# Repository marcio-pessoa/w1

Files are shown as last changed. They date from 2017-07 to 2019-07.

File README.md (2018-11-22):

# w1 Mark I - Watch Winder

## Introduction
**w1m1** is an acronim to Watch Winder with One slot - Mark I.

A watch winder is a device used to keep automatic watch running when not worn. Automatic watches operate on the principle of winding themselves using a moving weight inside the watch. The weight swings or rotates while the watch is worn and turns the winding mechanism inside the watch. So, fairly obviously, if the watch is not worn, then it no longer receives power this way and will run down. While virtually all automatic watches can be manually wound, this is not always convenient. So the concept of an automatic watch winder was born.

A winder cannot over wind an automatic watch, since all automatic watches have a special mainspring that will never come to the end of the spring. Most winders are on some sort of a timer, so they will operate for a few minutes, then “rest” for a bit, then start their motion again.  There is no need to keep the watch in motion 24 hours.

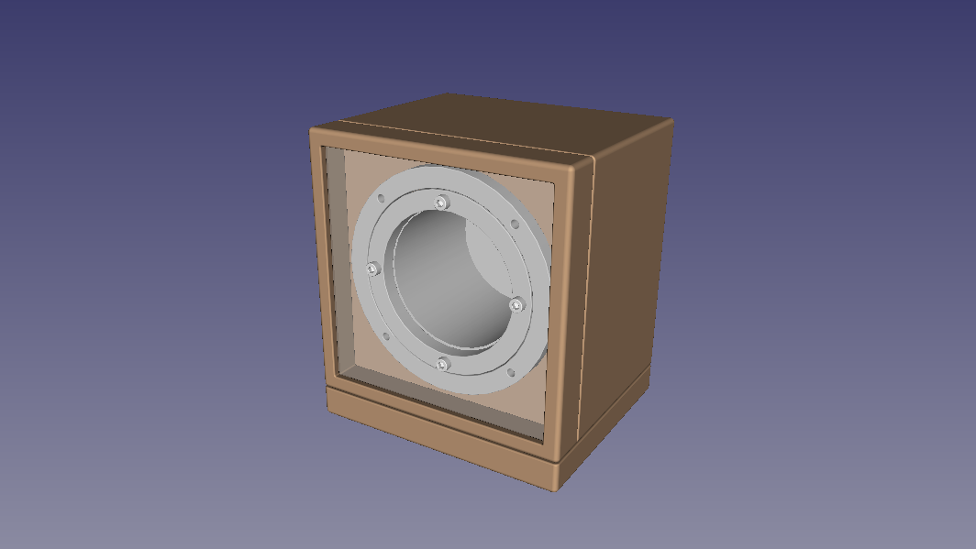
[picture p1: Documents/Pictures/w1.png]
Mechanical design


## Videos
Watch this projects videos on [YouTube Playlist].

## Changes
All notable changes to this project will be documented in this [Change log](CHANGELOG.md).

## Mechanics
This project uses an original mech made from scratch with the following goals:
- Reliable
- Noiseless
- Robust
- Well done
- Cheap, but very beautiful

Check out [Mechanics](Mechanics/README.md) design to know more.

## Electronics
Arduino Leonardo is used with other [Electronics](Electronics/README.md) parts to control the system.

## Firmware
A fully original [Firmware](w1/README.md) was developed to this project.

## BOM - Bill of materials
If you want to build your own, take a look at [Bill of materials](BOM.md).

---
[YouTube Playlist]: https://www.youtube.com/watch?v=WERBobZZHRU&list=PLs1JZHyVhlZXI1KqAdF2J8b70U7dsO11w

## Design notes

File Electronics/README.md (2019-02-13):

# w1 Mark I - Watch Winder

[Main page]

## Electronics

### Arduino
Technical specifications:
- Model: [Arduino Leonardo]

#### Diagram
                                 .-----.
    .----[PWR]-------------------| USB |--.
    |                            '-----'  |
    |                                     |
    |                           A5/SCL[ ] |   C5
    |                           A4/SDA[ ] |   C4
    |                             AREF[ ] |
    |                              GND[ ] |
    | [ ]NC                     SCK/13[ ]~|   B5
    | [ ]v.ref                 MISO/12[ ] |   .
    | [ ]RST                   MOSI/11[ ]~|   .
    | [ ]3V3   +-----+              10[ ]~|   .
    | [ ]5v    |     |               9[ ]~|   .
    | [ ]GND   | MCU |               8[ ] |   B0
    | [ ]GND   |     |                    |
    | [ ]Vin   +-----+               7[ ] |   D7
    |                                6[ ]~|   .
    | [ ]A0                          5[ ]~|   .
    | [ ]A1                          4[ ] |   .
    | [ ]A2                     INT1/3[ ]~|   .
    | [ ]A3                     INT0/2[ ] |   .
    | [ ]A4/SDA  RST SCK MISO     TX>1[ ] |   .
    | [ ]A5/SCL  [ ] [ ] [ ]      RX<0[ ] |   D0
    |            [ ] [ ] [ ]              |
    '--.                         .--------'
       \_______________________/

Arduino Leonardo diagram by http://busyducks.com/ascii-art-arduinos

#### Pin designation
 id | pin |   type    | direction |               description
----|-----|-----------|-----------|--------------------------------------------
  0 |   0 | digital   | input     | Serial communication
  1 |   1 | digital   | output    | Serial communication
  2 |   0 | -         | -         |
  3 |   1 | interrupt | input     | Speed sensor
  4 |   - | -         | -         | -
  5 |   5 | PWM       | output    | Motor (speed control)
  6 |   6 | PWM       | output    | Motor (speed control)
  7 |   - | -         | -         | -
  8 |   - | -         | -         | -
  9 |   9 | -         | -         | -
 10 |  10 | -         | -         | -
 11 |  11 | -         | -         | -
 12 |   - | -         | -         | -
 13 |  13 | PWM       | output    | Status LED
 14 |     | -         | -         | -
 15 |   - | -         | -         | -
 16 |   - | -         | -         | -
 17 |   - | -         | -         | -
 18 |   - | -         | -         | -
 19 |   - | -         | -         | -

### Motor
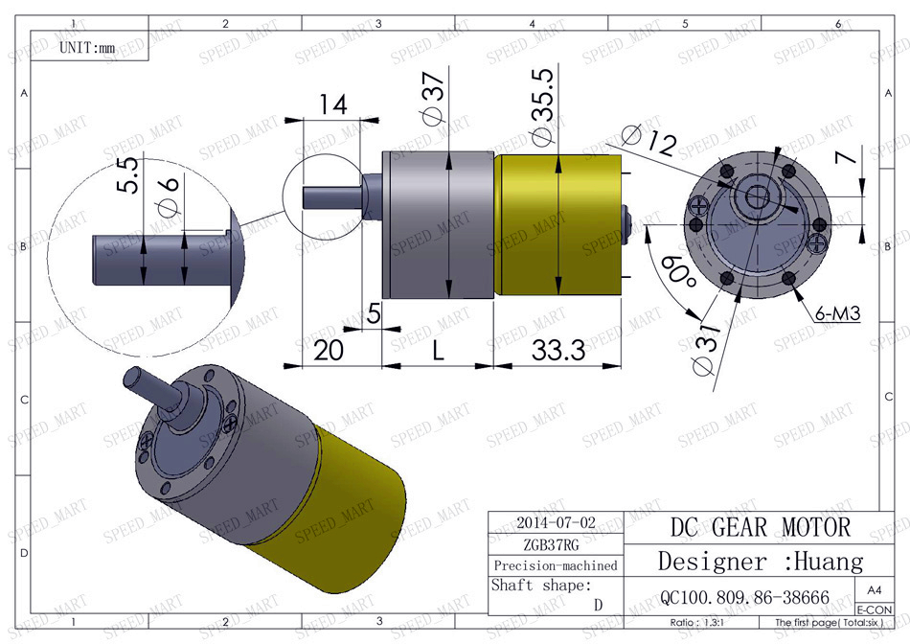
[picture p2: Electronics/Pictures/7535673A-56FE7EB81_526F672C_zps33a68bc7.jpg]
Gear motor


Reversible 37mm 12V DC 100RPM Gear-Box Speed controlled.

Technical specifications:
- Model: ZGB37RG
- Shaft speed: 100 RPM
- Rotor Speed: 5000r/min
- Reversibility: yes
- Voltage: 12V DC
- Current: 800mA (no load)
- Torque: 4kg/cm
- Diameter: 37mm
- Shaft length: 15mm
- Shaft diameter: 6mm

#### Driver
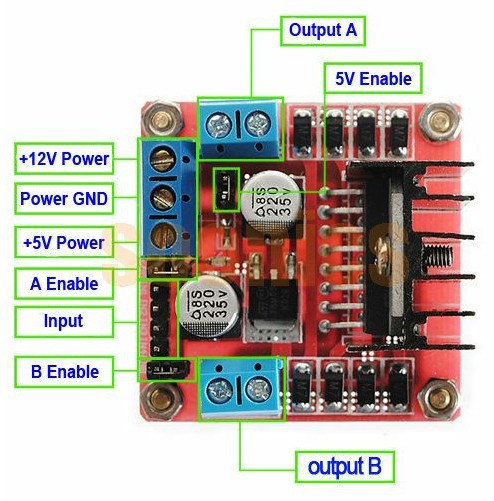
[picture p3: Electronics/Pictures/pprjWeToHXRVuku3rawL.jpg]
L298 motor driver


> "The L298 is an integrated monolithic circuit in a 15-lead Multiwatt and Power SO20 packages. It is a high voltage, high current dual full-bridge driver designed to accept standard TTL logic levels and drive inductive loads such as relays, solenoids, DC and stepping motors. Two enable inputs are provided to enable or disable the device independently of the input signals. The emitters of the lower transistors of each bridge are connected together and the corresponding external terminal can be used for the connection of an external sensing resistor. Anadditional supply input is provided so that the logic works at a lower voltage."
>
> -- From: [L298](../Documents/L298.pdf) data book

L298N absolute maximum ratings:

 Symbol   | Parameter                              | Value      | Unit
----------|----------------------------------------|------------|--------------
 Vs       | Power Supply                           |         50 | V
 Vss      | Logic Supply Voltage                   |          7 | V
 Vi,Ven   | Input and Enable Voltage               |  -0.3 to 7 | V
 Io       | Peak Output Current (each Channel)     |          2 | A
 Vsens    | Sensing Voltage                        |  -1 to 2.3 | V
 Ptot     | Total Power Dissipation (Tcase = 75°C) |         25 | W
 Top      | Junction Operating Temperature         | -25 to 130 | °C
 Tstg, Tj | Storage and Junction Temperature       | -40 to 150 | °C

#### Revolution sensor
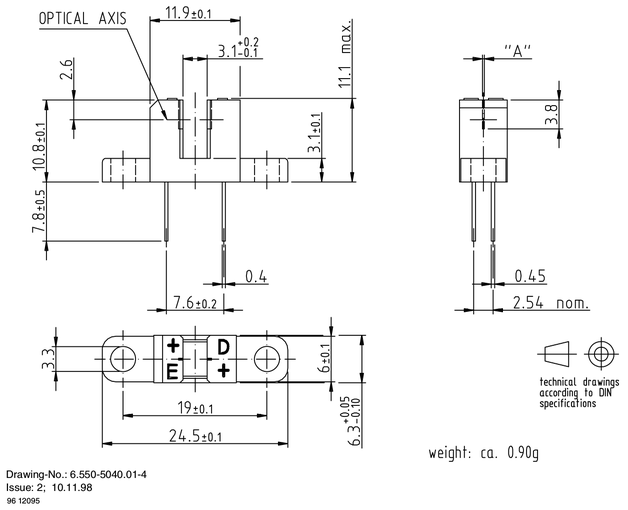
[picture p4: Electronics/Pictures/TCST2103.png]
TCST2103 sensor


> "The TCST2103 is a transmissive sensor that include an infrared emitter and phototransistor, located face-to-face on the optical axes in a leaded package which blocks visible light."
>
> -- From: [TCST2103](../Documents/TCST2103.pdf) data book

### Charger system

#### Qi

### Door sensor
Technical specifications:
- Model: Sensor 44E_938
- Type: Magnetic

[Main page]

---

[Main page]: ../README.md
[Arduino Leonardo]: https://www.arduino.cc/en/Main/arduinoBoardLeonardo/#techspecs

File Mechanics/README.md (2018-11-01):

# w1 Mark I - Watch Winder

[Main page]

## Mechanics

### Case
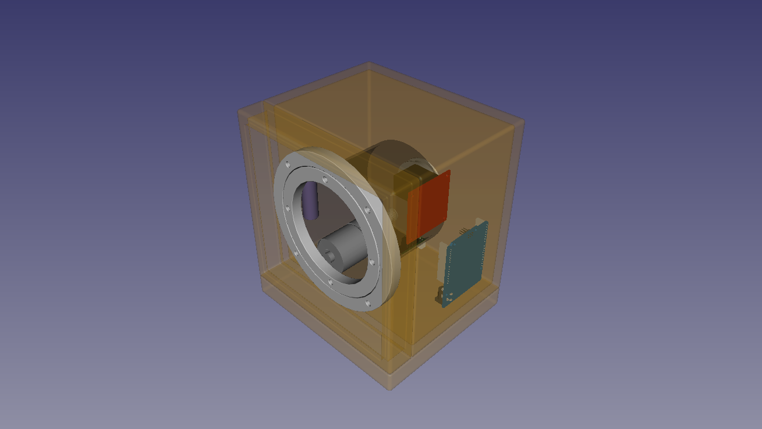
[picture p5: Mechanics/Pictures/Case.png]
Case


Technical specifications:
- Material: Wood
- Feature: Noise reduction with internal fine spounge

### Base
Base

Technical specifications:
- Material: Wood

#### Feet
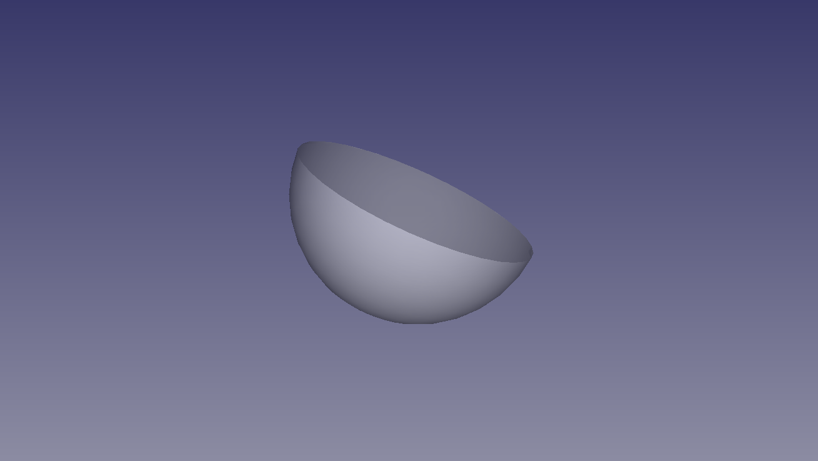
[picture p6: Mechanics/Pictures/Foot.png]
Foot


Technical specifications:
- Material: Silicone
- Feature: Self adhesive
- Color: Transparent
- Diameter: 8 mm
- Height: 2.5 mm

### Engine

#### Pulleys

##### Large
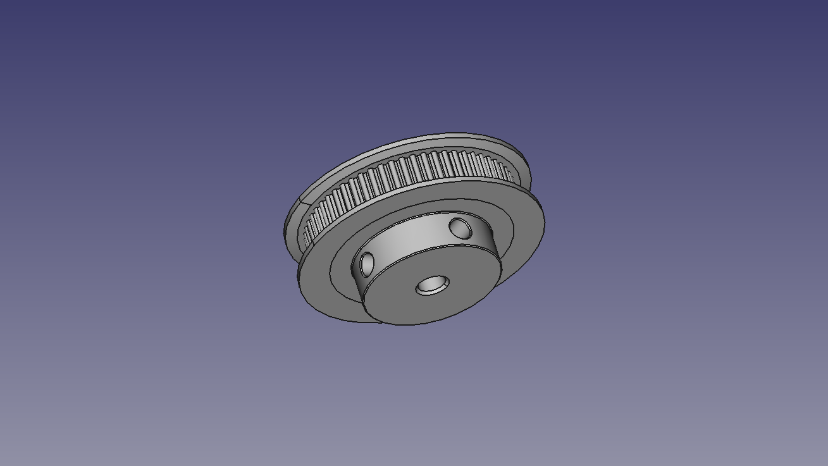
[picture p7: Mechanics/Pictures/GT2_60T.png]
GT2 60T


Technical specifications:
- Model: GT2-60T
- Bore 5mm
- Standard: GT2
- Pinch: 2 mm
- Teeth: 60 T
- Material: Aluminium

##### Small
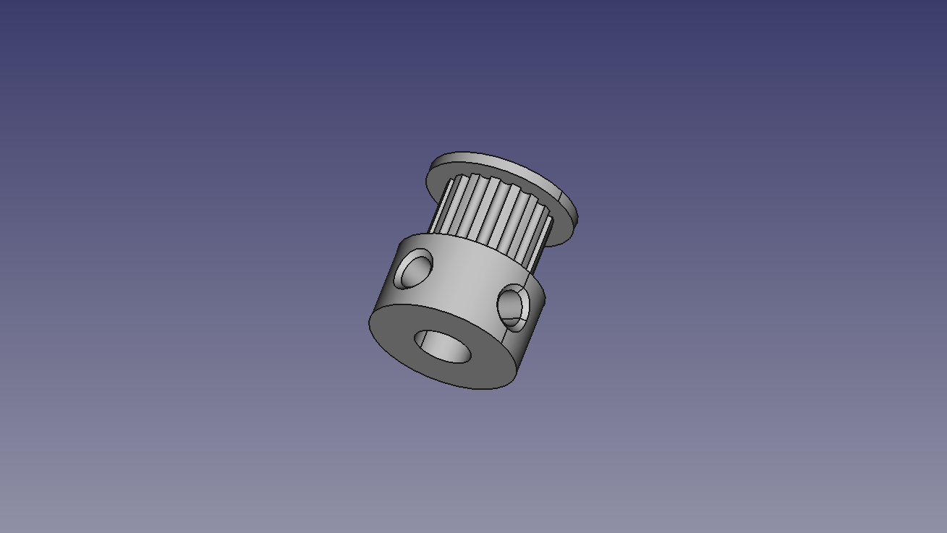
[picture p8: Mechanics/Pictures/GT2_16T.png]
GT2 16T


Technical specifications:
- Model: GT2-16T
- Bore 6mm
- Standard: GT2
- Pinch: 2 mm
- Teeth: 16T
- Material: Aluminium

#### Pulleys relationship
Calculating pulleys relantionship:

$$ s = \frac{B . 100}{A} \% $$

Where:
- A: Large pulley = 60T (Rotor Pulley)
- B: Small pulley = 16T (Motor Pulley)
- s: Speed Ratio = ?

$$ s = \frac{16 . 100}{60} \% $$

So:
$$ s = 26.7 \% $$

#### Wheelbase
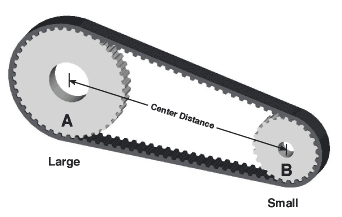
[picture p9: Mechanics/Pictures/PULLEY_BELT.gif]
Center distance


Use trigonometric functions to calculate distance between points A and B.

Using the Pi constant and pulley sizes, it is possible to calculate the belt size and the number of teeth.

Wheelbase data:
- Large pulley (A): 38.2 mm
- Small pulley (B): 10.2 mm
- Center distance: **64.5 mm**
- Teeth in mesh: **6 T**

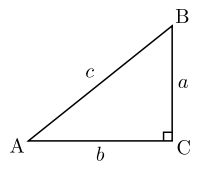
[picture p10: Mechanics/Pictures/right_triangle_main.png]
Right triangle


Reference: https://www.bbman.com/belt-length-calculator/

#### Belt
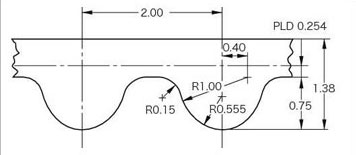
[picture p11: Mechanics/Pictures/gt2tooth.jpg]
GT2 belt


Technical specifications:
- Standard: GT2
- Pinch: 2 mm
- Wide: 6 mm
- Internal lenght: 208 mm
- Teeth: 104 T

#### Lazy Susan
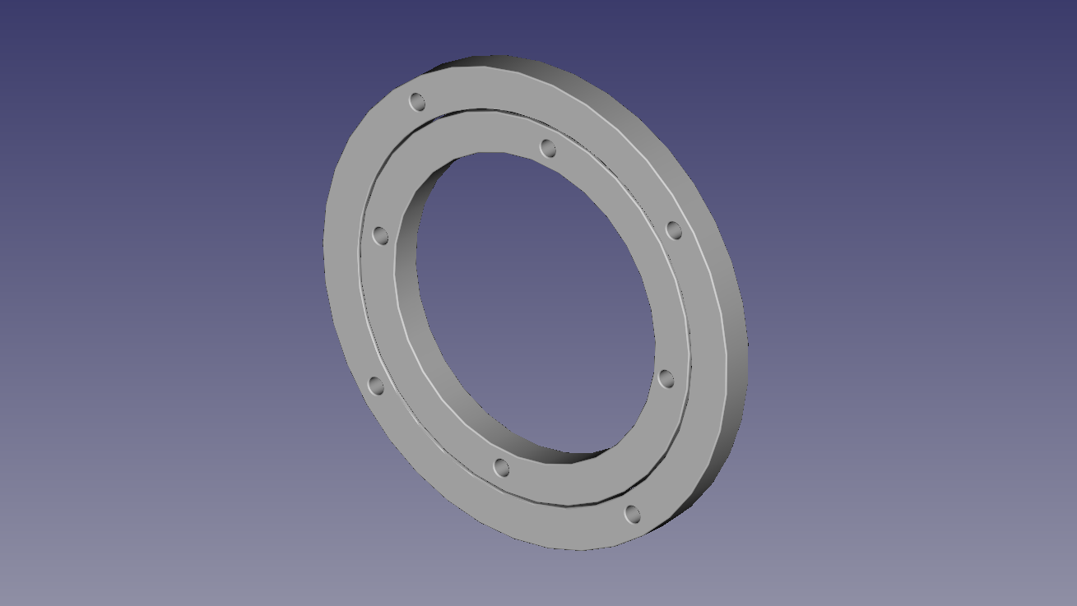
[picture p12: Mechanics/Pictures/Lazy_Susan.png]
Lazy Susan


Technical specifications:
- Material: aluminium
- Move: bearing 
- External diameter: 140 mm
- Internal diameter: 90 mm

#### Cup
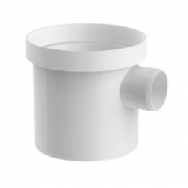
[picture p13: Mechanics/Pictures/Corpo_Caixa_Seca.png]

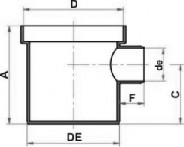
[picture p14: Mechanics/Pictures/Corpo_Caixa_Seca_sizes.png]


Technical specifications:
- Material: PVC
- A: 100 mm
- C: 60.6 mm
- D: 101.6 mm
- DE: 94 mm
- F: 24.8 mm
- de: 37.5 mm

[Main page]

---

[Main page]: ../README.md

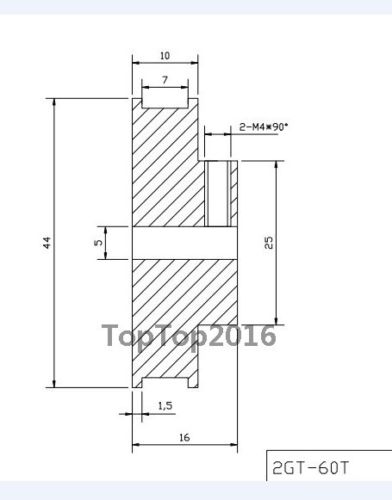
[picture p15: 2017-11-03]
Mechanics/Pictures/GT2 60T.jpg

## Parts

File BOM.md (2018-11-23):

# BOM
w1 Mark I - Watch Winder, Bill of materials

## Purchased
| Quant | Description | ID | Bought | Delivered  | Unit | Charge | Taxes | Cost |
|---|---|---|---|---|---|---|---|---|
| 1 | Arduino_Leonardo | 282612975059 | 2017-08-21 | 2017-10-dd | each | 6.50 |  0.41 | 6.91 |
| 1 | L298N | 192067670930 | 2017-08-21 | 2017-11-dd | each | 1.63 |  0.10 | 1.73 |
| 1 | GT2-16T | 332299393077 | 2017-11-04 | 2017-11-dd | each | 1.99 |  0.13 | 2.12 |
| 1 | GT2-60T | 322570479070 | 2017-08-28 | 2017-mm-dd | each | 3.32 |  0.20 | 3.52 |
| 1 | Lazy_Susan_140mm | 292120279850 | 2017-07-24 | 2017-08-31 | each | 7.14 |  0.44 | 7.58 |
| 1 | GT2_104T_Belt | 162212717993 | 2017-07-27 | 2017-09-19 | each | 2.08 |  0.13 | 2.21 |
| 1 | TCST2103 | 381842310412 | 2016-12-22 | 2017-05-18 | each | 0.80 |  0.05 | 0.85 |
| 1 | ZGB37RG | 261642131158 | 2016-12-26 | 2017-11-01 | each |  15.99 |  1.01 |  17.00 |
| 1 | Platic_cup | - | 2018-01-26 | 2018-01-26 | each | 2.82 |  0.00 | 2.82 |
| 1 | Magnet | - | 2015-mm-dd | 2015-mm-dd | each | 0.00 |  0.00 | 0.00 |
| 1 | Battery | 261530668000 | 2015-05-05 | 2015-mm-dd | each | 1.11 |  0.06 | 1.17 |
| 1 | Battery_case | 263210608095 | 2017-12-03 | 2018-03-29 | each | 0.78 |  0.05 | 0.83 |
| 1 | Qi_receiver | 312013493657 | 2017-12-04 | 2018-04-07 | each | 1.90 |  0.11 | 2.01 |
| 1 | 44E_938 | 181262049602 | 2018-01-01 | 2018-04-18 | each | 0.93 |  0.06 | 0.99 |
| 4 | Silicone_Feet | 182933353181 | 2017-12-27 | 2018-05-28 | each | 0.04 |  0.01 | 0.05 |
| 1 | Qi_charger | 122959306322 | 2018-02-13 | 2018-04-24 | each | 2.83 |  0.17 | 3.00 |
| 1 | Case | - | 2018-04-30 | 2018-04-30 | each | 1.00 |  0.00 | 1.00 |
| 1 | Screw_M5x25mm | 222714655541 | 2017-12-23 | 2018-04-28 | each | 0.20 |  0.02 | 0.22 |
| 5 | Nut_M5_nylon | 222111255325 | 2017-04-25 | 2017-07-dd | each | 0.50 |  0.05 | 0.55 |
| 4 | T-slot_90_corner | 131977551173 | 2016-11-04 | 2016-mm-dd | each | 1.00 |  0.06 | 1.06 |
| 1 | Frame_134x114 | - | 2018-09-28 | 2018-09-28 | each | 0.99 |  0.00 | 0.99 |
| 1 | Frame_125x114 | - | 2018-09-28 | 2018-09-28 | each | 0.99 |  0.00 | 0.99 |
| 4 | T-slot_90*_joint | 163151502873 | 2018-08-18 | 2018-09-27 | each | 1.26 |  0.08 | 1.34 |
| 10 | Screw_M3x8mm_flat  | 253637575896 | 2018-09-30 | 2018-10-23 | each | 0.99 | | |
| 20 | Screw_M3x10mm_flat | 253637575896 | 2018-09-30 | 2018-10-23 | each | 1.07 | | |
| 10 | Screw_M5x20mm_But. | 302874264440 | 2018-10-18 | 2018-11-09 | each | 2.37 | | |
| 1 | Acrylic_Sheet | 292062712986 | 2018-10-23 | 2018-11-19 | each | 6.28 | | |
| 1 | Base | Pending | Pending | pending | each | | | |
| 1 | Door | Pending | Pending | pending | each | | | |
| 1 | Door_glass | Pending | Pending | pending | each | | | |
| 1 | Sponge_adhesive | Pending | Pending | pending | each | | | |
| 1 | Velvet_feet | Pending | Pending | pending | each | | | |

Currency: USD

International IOF: 6.38%
Domestic IOF: 0.38%

Total cost: $58.94

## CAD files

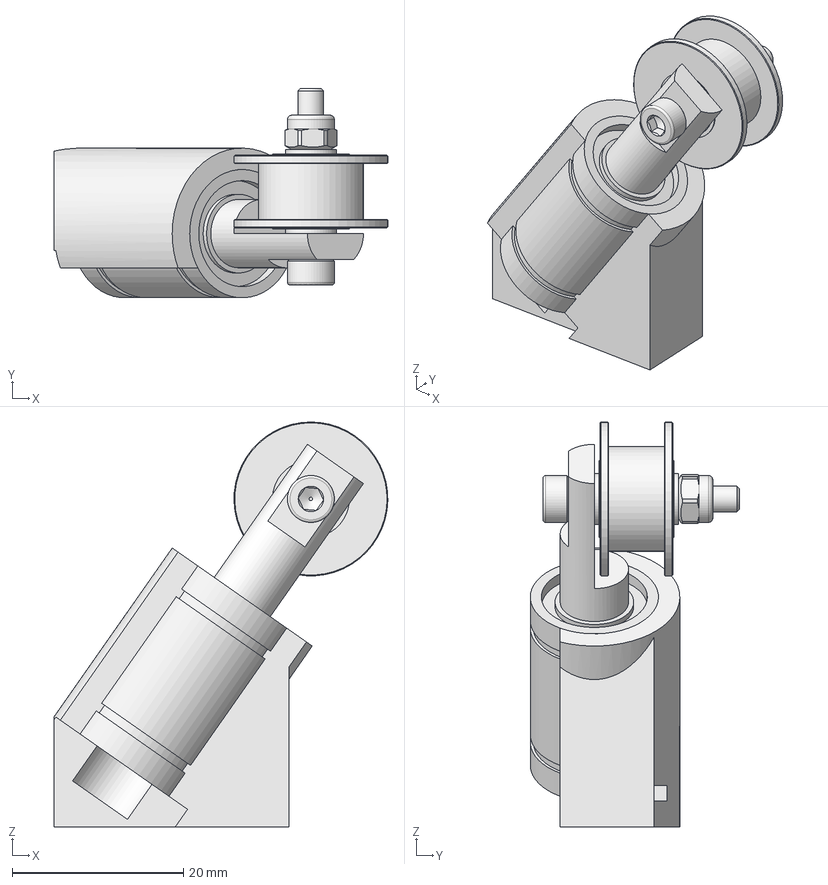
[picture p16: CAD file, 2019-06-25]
Mechanics/Linear_GT2_Belt_Tensioner.FCStd
39.0 x 24.5 x 47.4 mm
M3x20-Screw
M3-Washer_axis_in
M3-Nut_axis
M3-Washer
GT2 20T Smooth 5mm Bore
Piston
LM8UU
M3-Nut

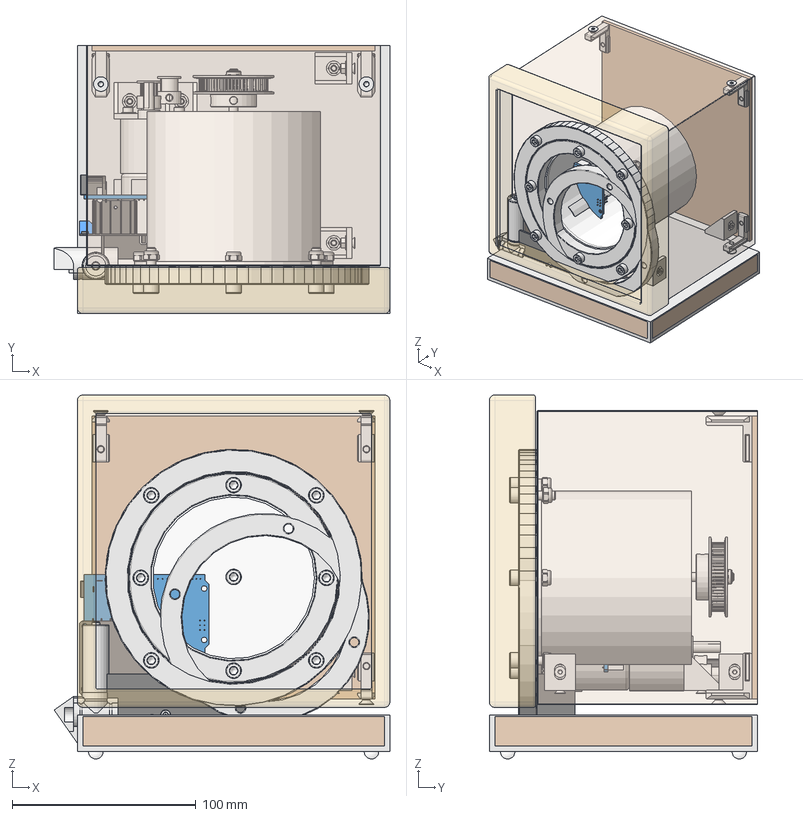
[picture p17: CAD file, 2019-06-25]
Mechanics/w1.FCStd
182.6 x 146.0 x 198.1 mm
Foot_001
Foot_002
Foot_003
Foot_004
CloneScrew001
CloneScrew002
CloneScrew003
CloneScrew004
CloneScrew005
CloneScrew006
CloneScrew007
CloneScrew008
Screw_001
Screw_002
Screw_003
Screw_004
Nut_001
Nut_002
Nut_003
Nut_004
Washer_001
Washer_002
Washer_003
Washer_004
Washer_005
Washer_006
Washer_007
Washer_008
Screw_006
Screw_005
Screw_008
Screw_007
Nut_007
Nut_008
L_005
L_004
L_001
L_002
M5-Nut_000
M5-Nut_001
M5-Nut_002
M5-Nut_003
M5-Nut_004
M5-Nut_005
M5-Nut_006
M5-Nut_007
M5-Nut_008
R6_bat
GT2 20T Smooth 5mm Bore
GT2 16T
GT2 16T_001
Piston
Base_001
Lazy Suzan In Fillet
Lazy Suzan Out Fillet
Door_
Lazy_Susan
Cup
M3-Nut_axis
10 pins-019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

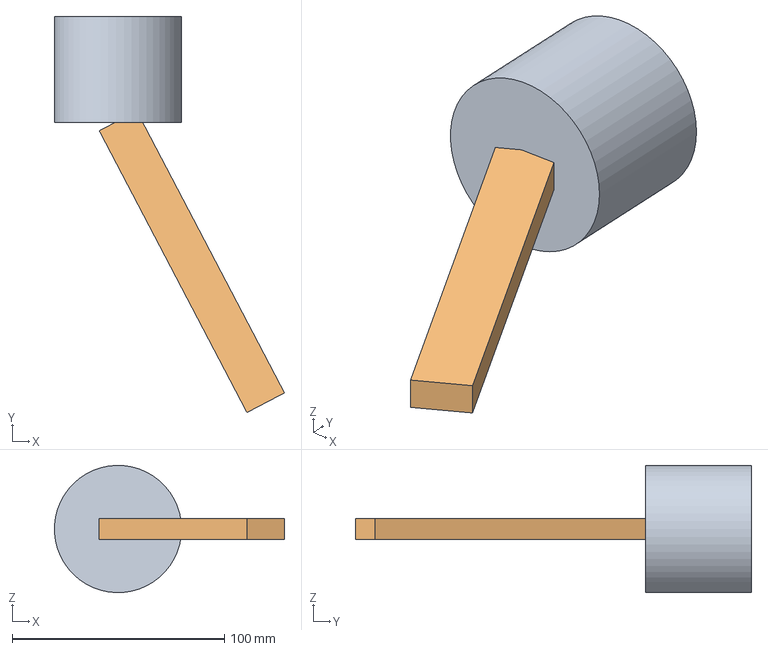
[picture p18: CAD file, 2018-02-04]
Mechanics/crank.FCStd
108.4 x 186.8 x 60.0 mm

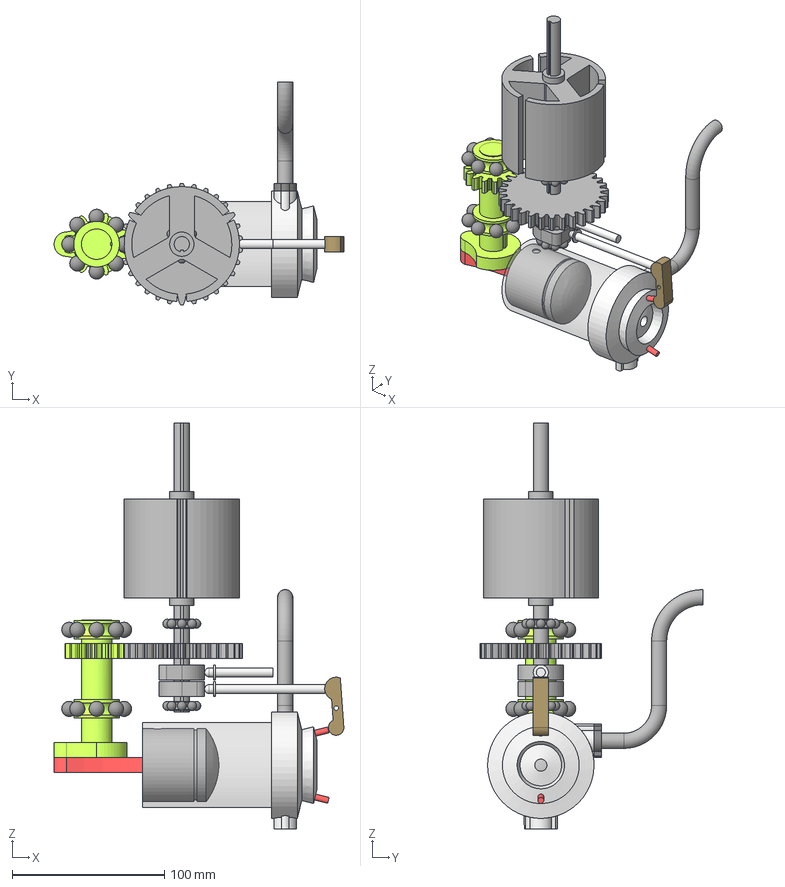
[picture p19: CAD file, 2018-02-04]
Mechanics/Mechanism.FCStd
190.6 x 146.7 x 267.0 mm
MainCylinder
PistonFinal
ConnRodFinal
Balls1
MainShaft
Balls2
HeadFinal
ScapeValve
IntakeValve
SecondaryShaft
Valve2RodFinal
Pipe
PipeHolder
Valve1RodFinal
ExaustValveLeverFinal

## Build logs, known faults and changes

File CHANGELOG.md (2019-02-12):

# CHANGELOG
w1 Mark I - Watch Winder, Change log

## [0.4] - 2017-12-26
### Added
- S command to set rotor speed.

## [0.4] - 2017-12-26
### Fixed
- Minor updates.

## [0.3] - 2017-11-12
### Fixed
- Minor updates.

## [0.2] - 2018-10-22
### Fixed
- Minor updates.

## [0.1] - 2017-11-04
### Added
- Working prototype.

## [0.0] - 2017-07-21
### Added
- The idea.

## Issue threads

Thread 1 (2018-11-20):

M3

marcio-pessoa, 2018-11-20:

marcio-pessoa, 2018-11-20:
This command isn't working properly:
```
M3
Rotor direction: Rotor speed: 100.00 %
nok
```

marcio-pessoa, 2018-12-27:
Problem fixed.

Closed 2018-12-27.

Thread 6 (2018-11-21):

Mechanics - Motor - Fix T-slot_90_corner

marcio-pessoa, 2018-11-21:

Closed 2018-12-27.

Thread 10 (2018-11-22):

Mechanics - Belt - Stress

marcio-pessoa, 2018-11-22:

marcio-pessoa, 2018-12-28:
Quando estava concluindo o Issue #34 percebi que seria necessário um tensionador.

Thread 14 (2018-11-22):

Mechanics - Frame - Design - Fix battery size

marcio-pessoa, 2018-11-22:

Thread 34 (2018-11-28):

Mechanics - Belt - Install

marcio-pessoa, 2018-11-28:

marcio-pessoa, 2018-11-28:
O eixo do rotor se mostrou estar excêntrico.
Com as ferramentas e material disponíveis, é pouco provável refazer o rotor com o eixo de rotação centralizado perfeitamente.
Será necessário usar um tensionador na correia.

Closed 2018-12-27.

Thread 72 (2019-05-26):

Mechanics - Motor support needs fix

marcio-pessoa, 2019-05-26:
O suporte precisa ser levemente modificado para permitir que o motor possa ser ajustado com maior amplitude, permitindo assim um maior tensionamento da correia.

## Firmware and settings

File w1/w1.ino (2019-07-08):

/* w1.ino, w1 Mark I - Watch Winder, Arduino main sketch file
 *
 * This sketch was developed and tested on: Arduino Leonardo
 * To work on other Arduino models, some adaptations may be necessary.
 *
 * Author: Márcio Pessoa <marcio.pessoa@gmail.com>
 * Contributors: none
 */

#include <Arduino.h>         // Arduino - Main library
#include <Project.h>         // Marcio Pessoa - Basic project definitions
#include <Timer.h>           // Marcio Pessoa - Timer with nice features
#include <SigGen.h>          // Marcio Pessoa - Signal Generator
#include <Alarm.h>           // Marcio Pessoa - Manage alarms
#include <L298.h>            // Marcio Pessoa - L298 DC motor control
#include "config.h"          // Marcio Pessoa - Configuration
#include <MemoryFree.h>      //

// Project definitions
Project w1("w1",  // Platform
           "I",  // Mark
           "Watch Winder",  // Name
           "0.4",  // Version
           "2019-02-12",  // Version date
           "7",  // Serial number
           "Copyright (c) 2017-2019 Marcio Pessoa",  // Owner
           "undefined. There is NO WARRANTY.",  // License
           "https://github.com/marcio-pessoa/w1",  // Website
           "Marcio Pessoa <marcio.pessoa@gmail.com>");  // Contact

// LEDs
SigGen wave;

// Check timer
Timer health_check(health_check_timer * 1000);

// Sensors timer
Timer sensors_status(sensors_timer * 1000);

// Axis
L298 motor;

void setup() {
  // Serial interface
  Serial.begin(serial_speed);
  // Start up message
  CommandM92();  // System information
  // Status LED
  pinMode(led_status_pin, OUTPUT);
  analogWrite(led_status_pin, LOW);
  // Motor
  motor.attach(in1_pin, in2_pin);
  CommandM2(motor_speed);  // Run rotor counterclockwise at default speed
  // Spin sensor
  pinMode(spin_sensor_vcc_pin, OUTPUT);
  pinMode(spin_sensor_gnd_pin, OUTPUT);
  digitalWrite(spin_sensor_vcc_pin, HIGH);
  digitalWrite(spin_sensor_gnd_pin, LOW);
  pinMode(spin_sensor_pin, INPUT_PULLUP);
  attachInterrupt(spin_sensor_pin, spinCounter, RISING);
  // G-code ready to receive commands
  GcodeReady();
}

void loop() {
  SensorsHandler();
  HealthCheckHandler();
  NotificationHandler();
  AxesHandler();
  DemonstrationHandler();
  PowerHandler();
  GcodeCheck();
}

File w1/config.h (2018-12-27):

/* config.h, w1 Mark I - Watch Winder, Arduino project config file
 * 
 * Author: Márcio Pessoa <marcio.pessoa@gmail.com>
 * Contributors: none
 */

// LED
const byte led_status_pin = 13;

// Motor
const byte in1_pin = 5;
const byte in2_pin = 6;
byte motor_speed = 75;  // percent

// Timers
const byte health_check_timer = 2;  // seconds
const byte sensors_timer = 0.5;  // seconds

// Spin sensor
const byte spin_sensor_pin = 1;  // pin: Digital 3
const byte spin_sensor_vcc_pin = 2;
const byte spin_sensor_gnd_pin = 4;

// Debug mode
bool debug_mode = false;

// Serial speed: 4800, 9600, 14400, 19200, 28800, 38400, 57600, 115200
const unsigned long serial_speed = 9600;

// 
const int FLIMIT = 32767;

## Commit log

2017-07-21 2017-07-21 * Version: 0.0b * The idea.
    [w1.sch]
2017-11-04 Arduino code
2017-11-06 Updating with GT2 16T Bore 6mm Timing Pulley
2017-11-23 3D model
    [w1.fcstd]
2017-11-23 3D model easy to view
    [w1.stl]
2017-11-25 Arduino Leonardo
2017-12-24 Just renaming file extension
    [w1.fcstd]
2018-02-04 Minor updates.
    [Mechanism.FCStd, crank.FCStd]
2018-02-06 Update 'BOM.md'
2018-05-08 Minor updates
    [w1.FCStd]
